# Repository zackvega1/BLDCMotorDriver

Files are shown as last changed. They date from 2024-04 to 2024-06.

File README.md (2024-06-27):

# BLDCMotorDriver
This project heavily references the code seen in the [simpleFOC repository](https://github.com/simplefoc), but is modified to run on the [Raspberry Pi Pico](https://datasheets.raspberrypi.com/pico/pico-datasheet.pdf) using [PlatformIO](https://platformio.org/).

## Prototype BLDC Driver Board
Reference this link for the prototypical BLDC driver board developing during ROB 310 Winter 2024:
[BLDC Motor Driver Board](https://u.easyeda.com/account/user/projects/index/detail?project=8bae73a7920e45f9aaeda30bf190f509&listType=all)

Table of contents
=================
<!--ts-->

   * [IMPORTANT: USB driver](#important-usb-driver-to-flash-platformio-firmware-to-pi-pico)
   * [PlatformIO Setup](#platformio-setup)
   * [Results](#initial-testing-results)
<!--te-->

## IMPORTANT USB driver to flash PlatformIO firmware to Pi Pico 
If you don't do the following steps on your Pi Pico you'll likely encounter [this error](https://community.platformio.org/t/upload-error-1-on-pio-with-raspberry-pi-pico/36841).

1. Download the [Zadig USB driver installer](https://zadig.akeo.ie/)
2. Connect your Pico to your computer with a USB cable
3. Hold BOOTSEL on your Pico
4. Run Zadig and for RP2 Boot (Interface 1) install `libusb-win32 (v1.2.7.3)` or `WinUSB (v6.1.7600.16385)` \
   &rarr; we were able to get the firmware flashing to work with `libusb` but if you have issues try `WinUSB`
   

Once you have installed the USB driver of your choice on the Pico, perform the following steps when you want to reflash firmware:
1. Build your project in PlatformIO
2. Hold BOOTSEL on your Pico and power cycle
3. Manually drag `.pio/build/pico/firmware.uf2` to the mounted Pico drive

## PlatformIO Setup 

PlatformIO is the platform used to compile and build for the Raspberry Pi Pico. Follow the instructions below to install PlatformIO:

1. **Download [VSCode](https://code.visualstudio.com/download).**

2. **Open the Extension Manager:**
   
   Extension Manager

4. **Search for PlatformIO and install it:**
   
   Search for PlatformIO
   *Note: If you have not previously installed it, you'll see an "Install" button.*

5. **Restart VSCode.**
   Once restarted, you should see the PlatformIO icon on the left taskbar:

   PlatformIO Icon

6. **Confirmation:**
   If you see this icon, PlatformIO is successfully installed.

7. **For more information about PlatformIO, refer to the [documentation](https://platformio.org/).**

## Running the Code

1. **Clone or download the repository.**

2. **Open VSCode and click on the PlatformIO Icon.**

   PlatformIO Icon

4. **Your screen should look like this:**

   PlatformIO Screen

6. **Click on "Open Project".**
   
   Open Project

8. **Locate the directory where you saved your repository and click "Open".**
   *Note: Make sure to open the folder titled "BLDC".*

9. **PlatformIO will begin installing all necessary dependencies. This may take some time.**

10.**Once PlatformIO finishes installing everything click the build button in project tasks, this will compile the code. This will take a very long time on your first compile and be faster after that.**



### Place the Pico in BOOTSEL Mode by unplugging it, holding down the BOOTSEL button, then plugging it back in. You should see a mounted drive appear on your computer. 

11. **Go to the directory of repository. In the pico/build folder you should see a firmware.uft file once PlatformIO has finished buliding your code. Drag this to the pico**
12. **The Pico should then eject and your code will have been uploaded to the pico**

## Initial Testing Results

### Random Setpoint Position Control

https://github.com/zackvega1/BLDCMotorDriver/assets/79417604/a46cdf18-8f71-4b4d-b843-c2d0ab8e5b1c

### Sine Wave Trajectory

https://github.com/zackvega1/BLDCMotorDriver/assets/79417604/abbf2bf4-174d-46f4-b3fa-4214b0e3bb09

### Compliant Operation (Torque Limited)

https://github.com/zackvega1/BLDCMotorDriver/assets/79417604/30a29a10-5d14-485c-8b83-cfc31a08579d

## Single Motor Motor Driver Board

Schematic: 
SCH_SingleMotor_2024-06-26

Top Layer View:

3D_SingleMotor_2024-06-26

Contact `zvega` or `celwell20` for EasyEDA link

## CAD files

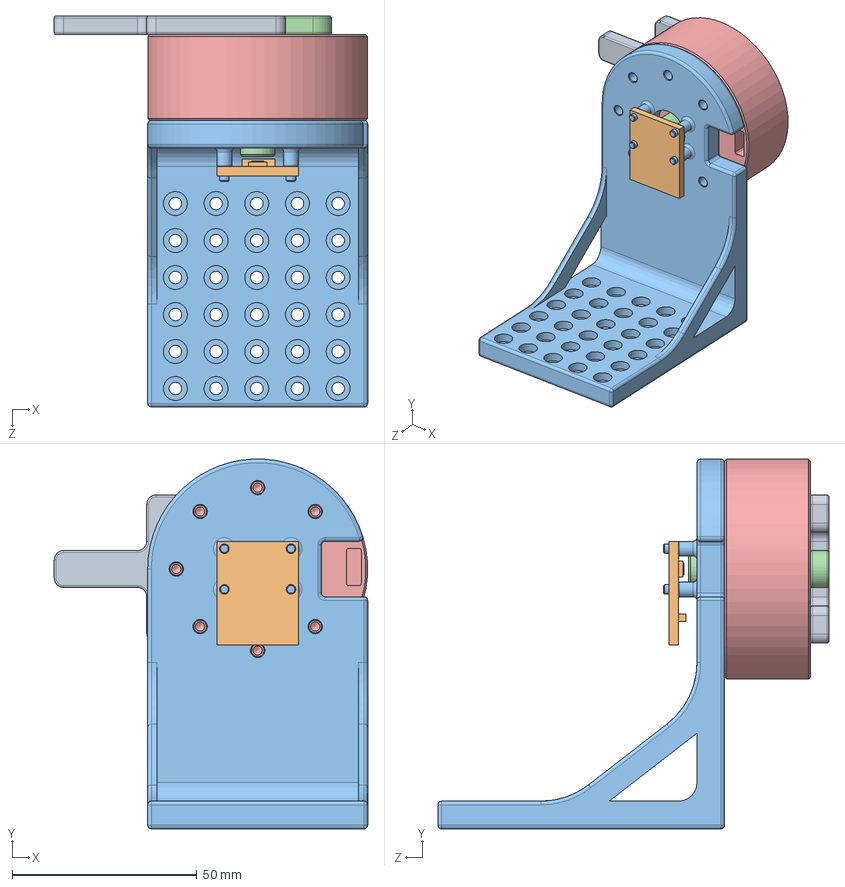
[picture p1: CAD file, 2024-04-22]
CAD/GM5208_CAD/GM5208__ENCODER_ASM.SLDASM
84.7 x 100.0 x 105.7 mm
GM5208-24_PART
GM5208_ROTOR_MAGNET_ADAPTER
GM5208_STATOR_ENCODER_ADAPTER
encoder_board
GM5208_TUNINGFORK

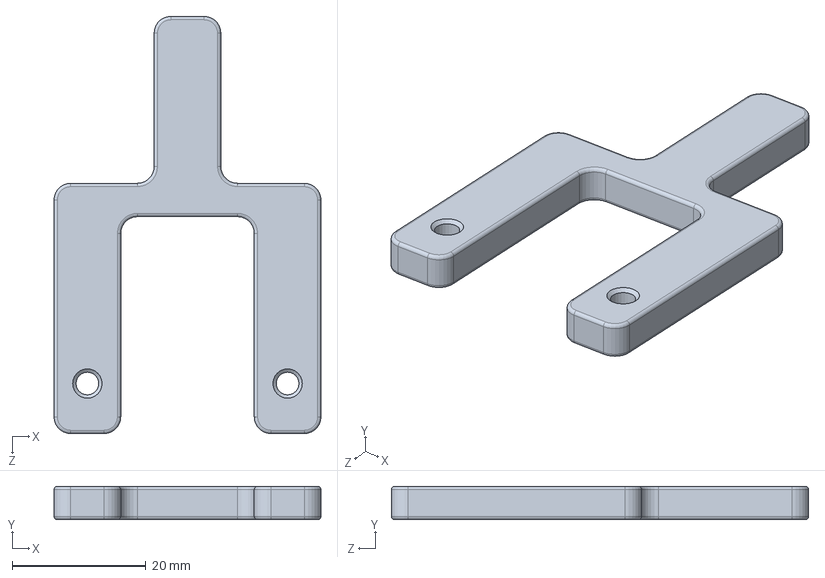
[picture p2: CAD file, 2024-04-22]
CAD/GM5208_CAD/GM5208_TUNINGFORK.SLDPRT
40.0 x 5.00 x 62.5 mm

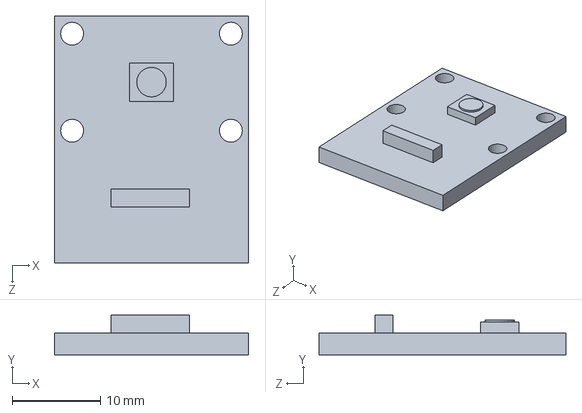
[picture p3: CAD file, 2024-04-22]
CAD/GM5208_CAD/encoder_board.SLDPRT
22.0 x 4.50 x 28.0 mm

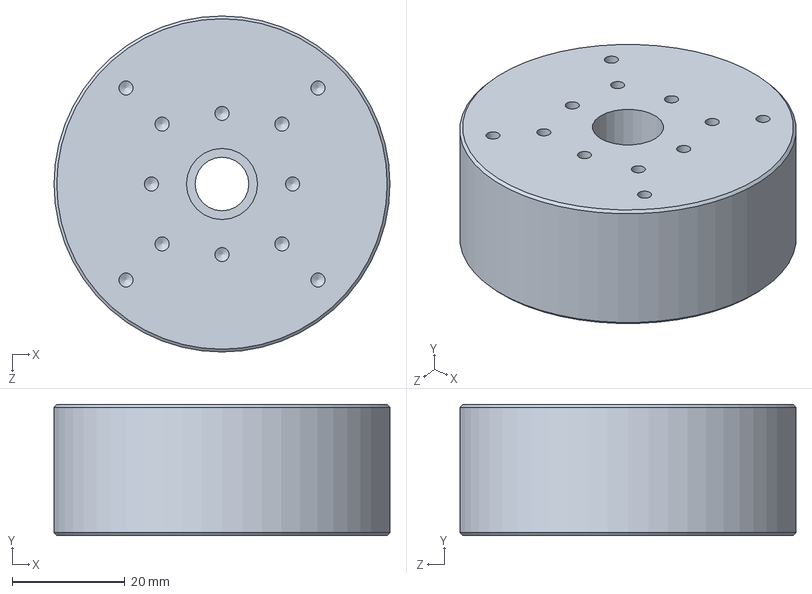
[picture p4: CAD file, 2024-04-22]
CAD/GM5208_CAD/GM5208-24_PART.SLDPRT
59.5 x 23.2 x 59.5 mm

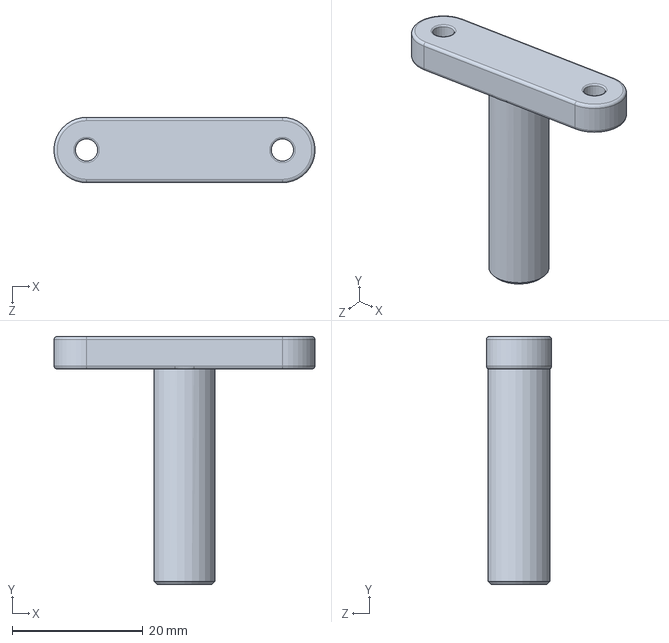
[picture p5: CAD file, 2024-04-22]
CAD/GM5208_CAD/GM5208_ROTOR_MAGNET_ADAPTER.SLDPRT
40.0 x 38.0 x 10.0 mm

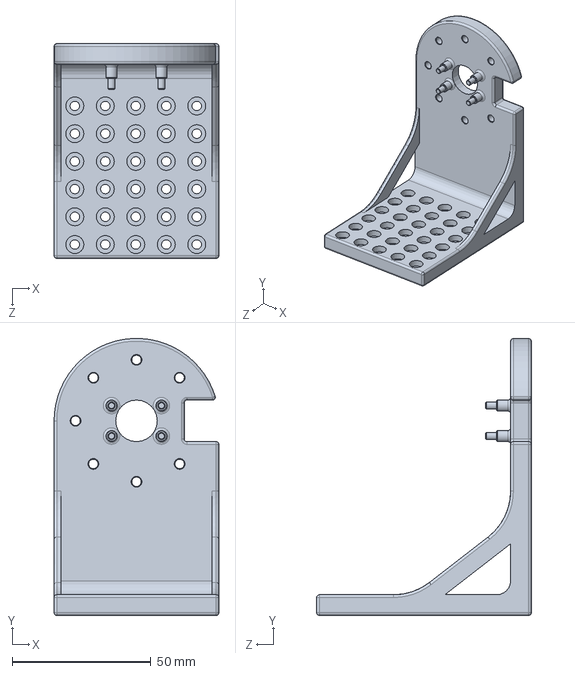
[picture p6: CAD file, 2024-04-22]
CAD/GM5208_CAD/GM5208_STATOR_ENCODER_ADAPTER.SLDPRT
59.5 x 100.0 x 77.5 mm

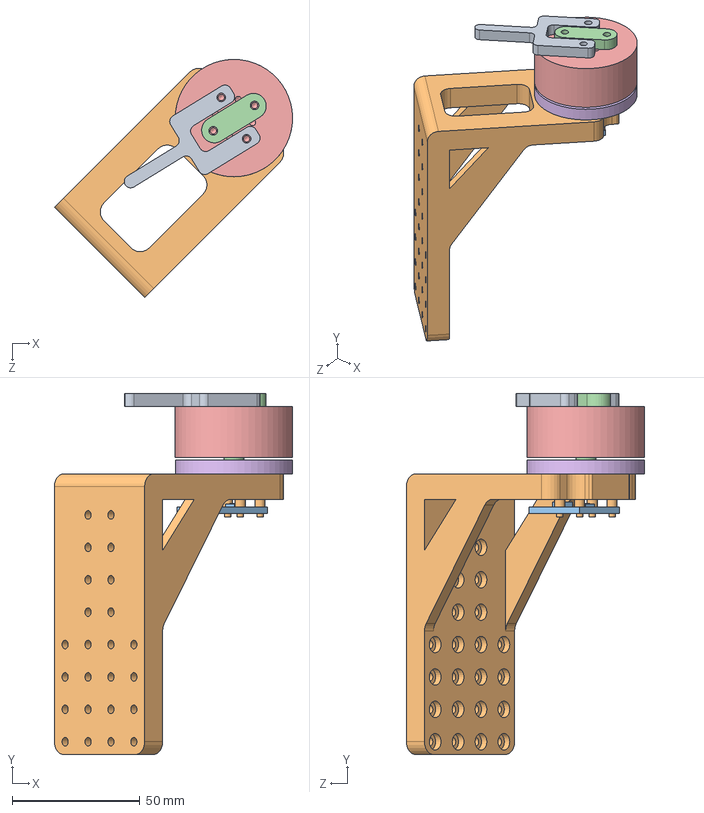
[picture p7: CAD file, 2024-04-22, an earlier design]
CAD/old_motor_cad/motor_encoder_assembly.SLDASM
93.4 x 141.5 x 93.4 mm
stator
rotor
magnet_mount
encoder_board
encoder_adapter_rev2
tuning_fork

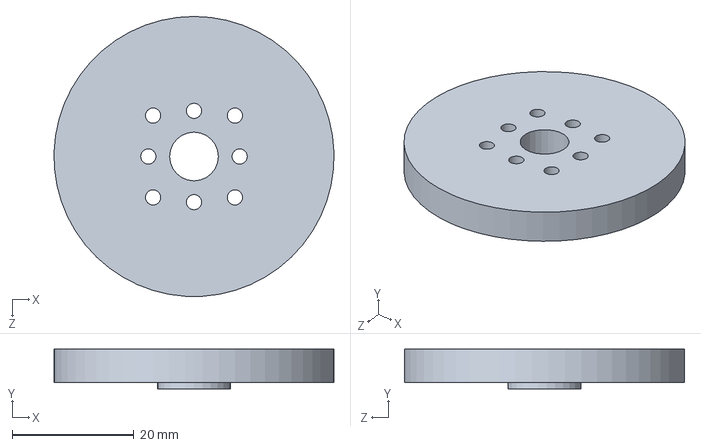
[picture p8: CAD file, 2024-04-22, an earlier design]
CAD/old_motor_cad/stator.SLDPRT
46.0 x 6.50 x 46.0 mm

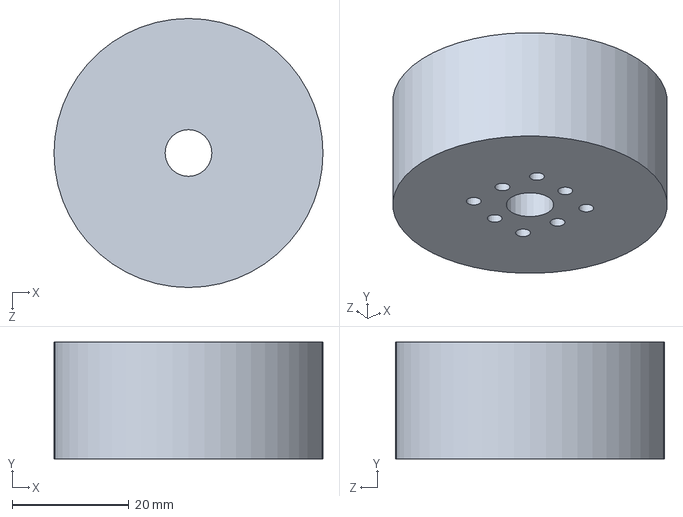
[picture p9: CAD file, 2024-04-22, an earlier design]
CAD/old_motor_cad/rotor.SLDPRT
46.0 x 20.0 x 46.0 mm

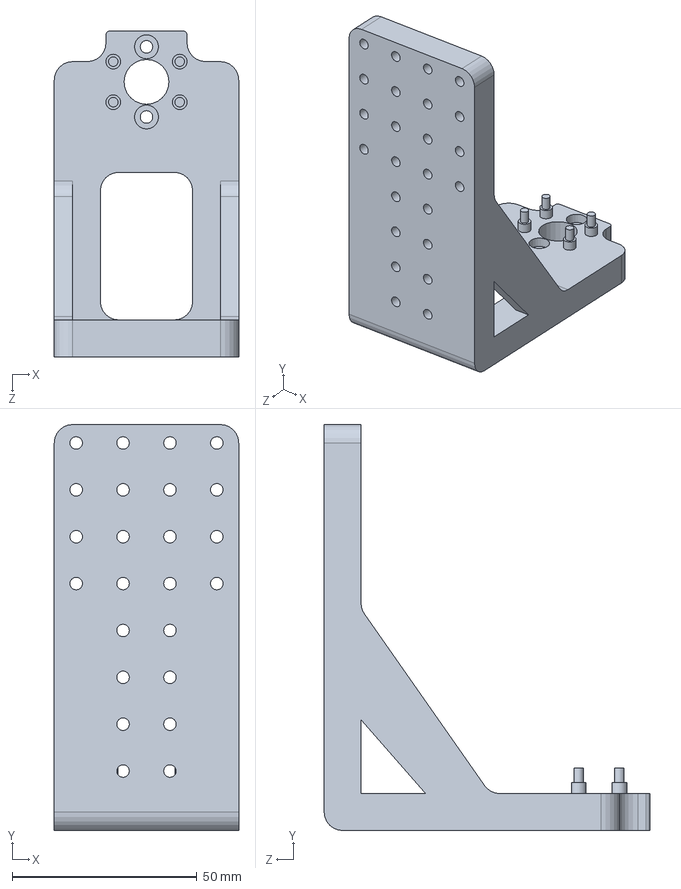
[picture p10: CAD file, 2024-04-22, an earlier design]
CAD/old_motor_cad/encoder_adapter_rev2.SLDPRT
50.0 x 110.0 x 88.2 mm

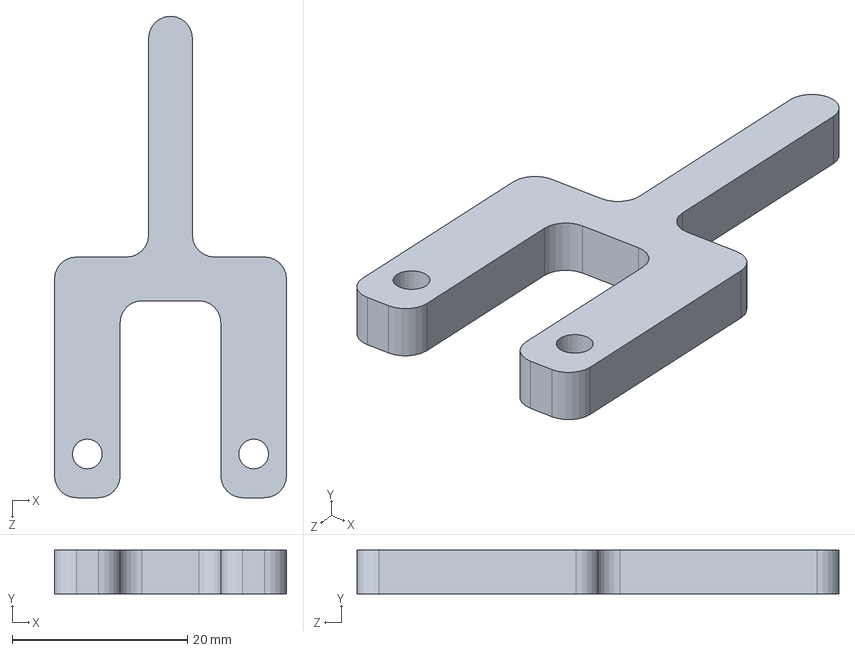
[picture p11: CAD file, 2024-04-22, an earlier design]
CAD/old_motor_cad/tuning_fork.SLDPRT
26.5 x 5.00 x 55.0 mm

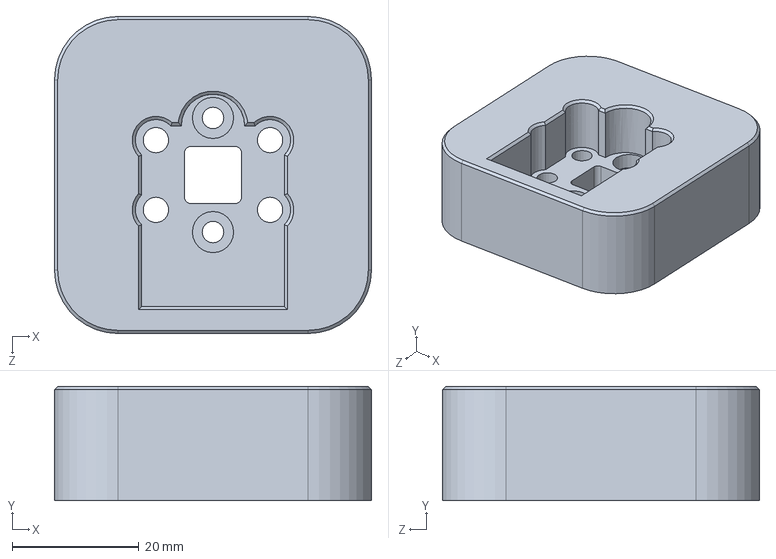
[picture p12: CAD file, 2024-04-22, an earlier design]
CAD/old_motor_cad/encoder_stator_adapter.SLDPRT
50.0 x 18.0 x 50.0 mm

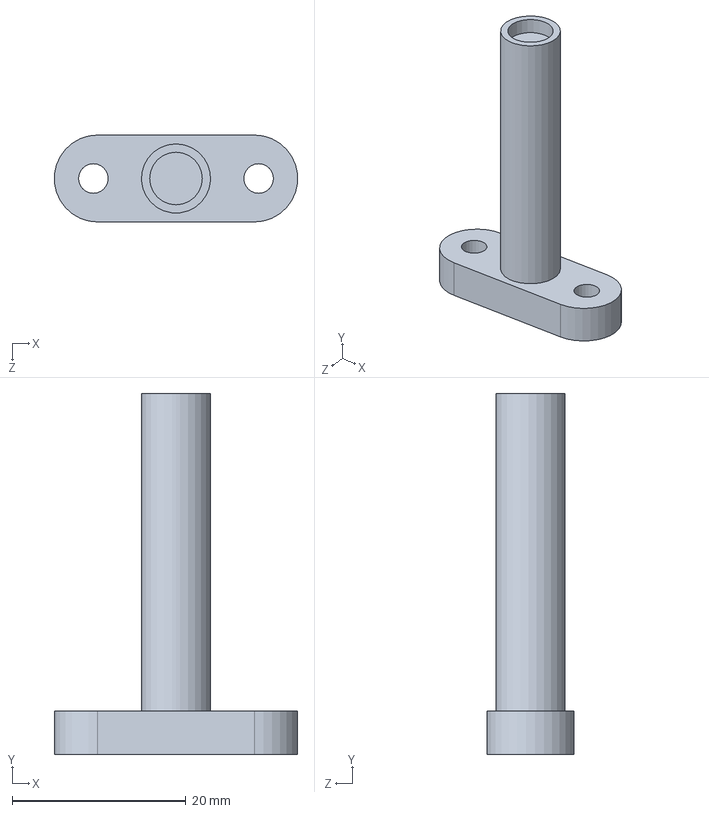
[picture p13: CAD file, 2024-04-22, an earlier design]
CAD/old_motor_cad/magnet_mount.SLDPRT
27.9 x 41.5 x 10.0 mm

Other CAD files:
CAD/GM5208_CAD/GM5208_ROTOR_MAGNET_ADAPTER.STL
CAD/GM5208_CAD/GM5208_STATOR_ENCODER_ADAPTER.STL
CAD/GM5208_CAD/GM5208_TUNINGFORK.STL

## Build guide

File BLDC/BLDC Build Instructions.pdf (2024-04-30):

Software Setup
Please follow the software setup instructions in our GitHub (https://github.com/zackvega1/BLDCMotorDriver) to update the drivers on the Pico properly, install PlatformIO, and run the code on the Pico. Be sure to update the drivers on the Raspberry Pico. Without this step, the project code will not work.

Hardware Assembly
Parts list for the BLDC Motor Driver Project:
- 1x AS5047 Magnetic Absolute Encoder
- 1x GM5208 Brushless Gimble Motor
- 1x Raspberry Pico
- 1x Brushless Bros Inc. PCB
- 1x 8-pin Wire Harness
- 1x 3-pin Wire Harness
- 1x power supply
- 1x 3D Printed Stator-Encoder Adapter
- 1x 3D Printed Rotor Magnet Adapter
- 1x 3D Printed “Tuning Fork”
- 1x 3D Printed PCB mount
- 8x 3M Bolts

Tools:
- Phillips Head Screwdriver
- Clamps (To clamp the motor mount to a table)

Instructions:
- 3D Print all necessary parts
- All CAD files can be found on our Github here (https://github.com/zackvega1/BLDCMotorDriver/tree/main/CAD/GM5208_CAD)
- All parts except the PCB mount and tuning fork were printed on a Form 2 Formlabs resin printer for dimensional accuracy
- The PCB mount and tuning fork were printed on an FDM Creality Ender 3
- Mount the Stator-Encoder Adapter to the GM5208 Motor’s stator using 4 10mm 3M bolts

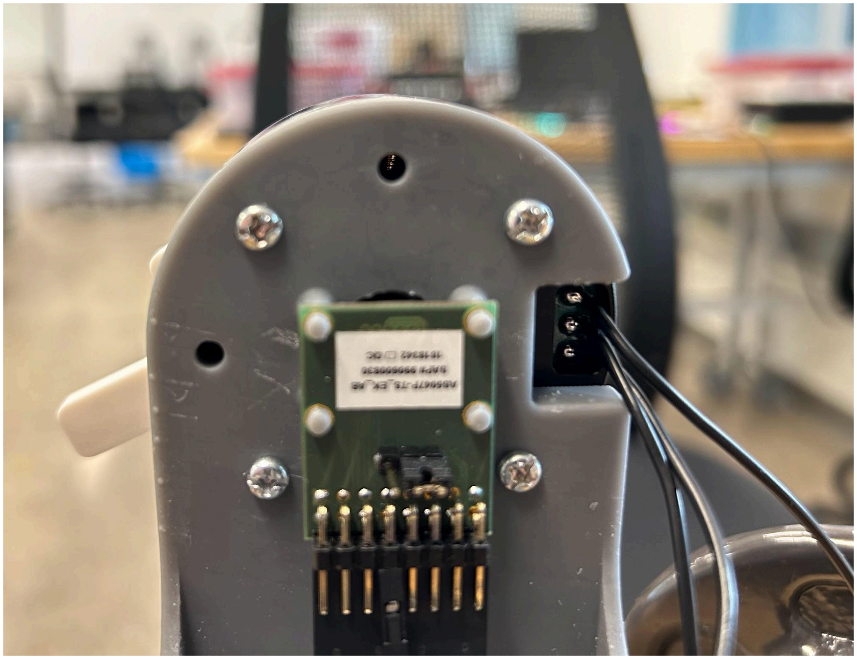
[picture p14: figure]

- Place the magnet disk for the encoder in the Rotor Magnet Adapter (press fit)
- Mount the Rotor Magnet Adapter to the GM5208 Motor’s rotor using 2 3M bolts
- Mount the Tuning Fork to the GM5208 Motor’s rotor using 2 3M bolts

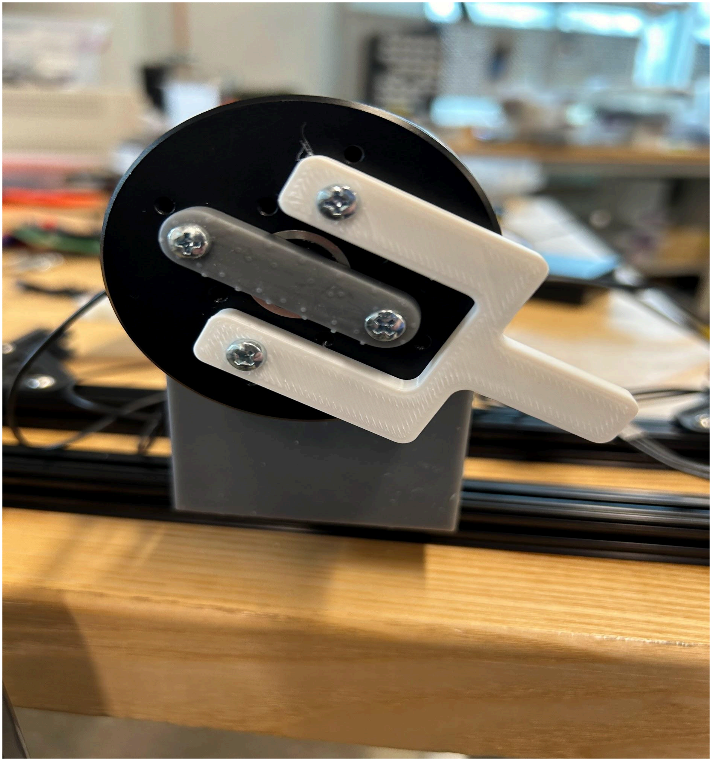
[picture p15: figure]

- Place the AS5047 Encoder chip on the Stator-Encoder Adapter by sticking the placement stubs through the mounting holes on the encoder chip
- Place the PCB board in the PCB mount
- Connect one side of the 8-pin wire harness to the bottom row of pins on the encoder chip (should have CSn, CLK, MISO, and MOSI pins along with power/ground pins)
- Connect the opposite side of the 8-pin wire harness to the PCB 8-pin female header pin connector

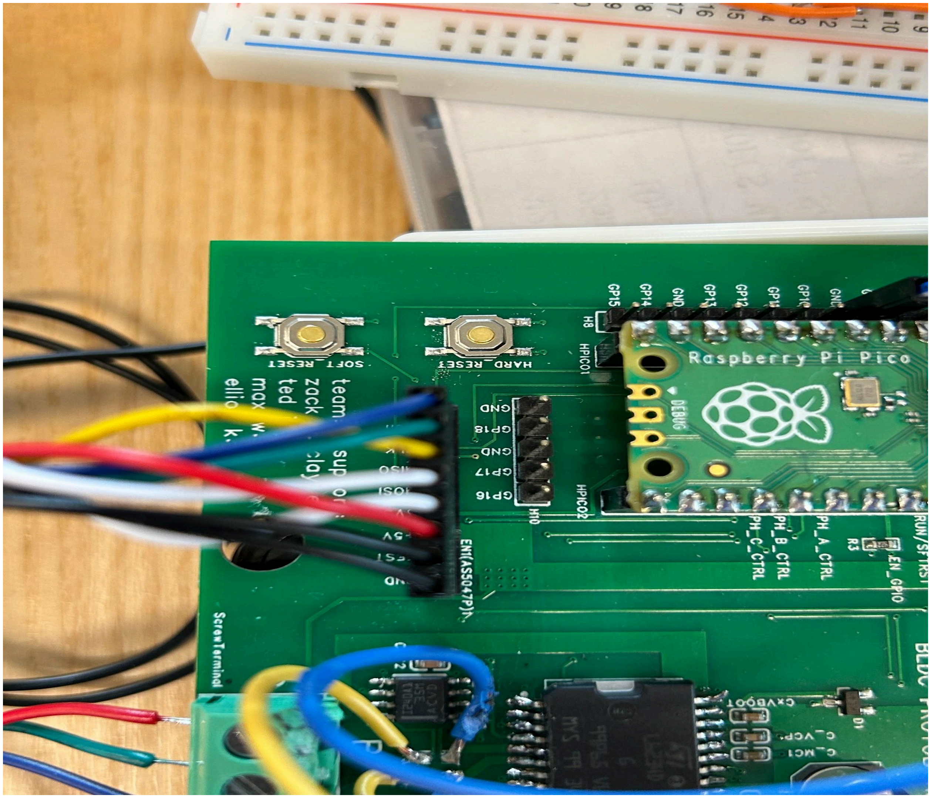
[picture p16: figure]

- Place the Raspberry Pico in the 20 female header pin connectors on the PCB
- Note about the PCB: our photos include the use of a breadboard wired to the PCB to replace resistors that had incorrect values during PCB production. If the shunt resistors R4 and R5 are 5 megaohms, this change will need to be made. If not, this change is not necessary. For the sake of brevity, we have left this change out of this document as it should not be necessary
- Connect the connector side of the 3-pin wire harness to the GM5208 wires
- Connect the opposite side of the 3-pin wire harness to the PCB by securing it in the 3-pin screw terminal

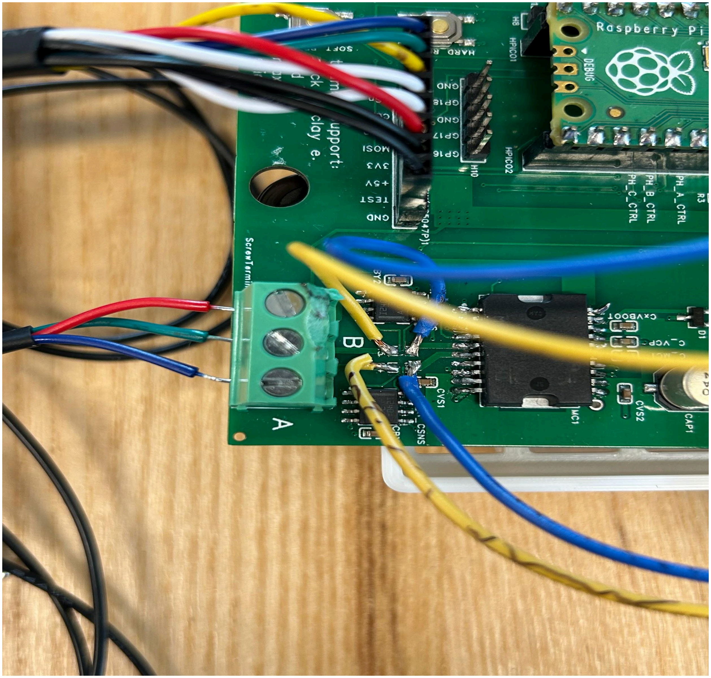
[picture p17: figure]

- Plug in the Power Supply (USB Battery) the barrel jack connector
- Connect micro USB cable to the Raspberry Pico for programming

Quick Startup
Once you’ve completed the software and hardware setup, pull the code from our GitHub to your local machine and set it up as a PlatformIO project. Follow the instructions in the software setup section to build the code and flash it onto the Raspberry Pico. The library of code will give you the ability to do velocity control or position control with this setup. In velocity control mode, you can set a speed setpoint and have the motor spin at the desired speed in (rad/s). In position control mode, you can set positional setpoints (in radians) and have the motor turn to those setpoints.

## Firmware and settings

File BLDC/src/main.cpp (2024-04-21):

#include "Arduino.h"
#include "SPI.h"
#include "SimpleFOC.h"
#include "SimpleFOCDrivers.h"
#include "encoders/as5047/MagneticSensorAS5047.h"


#define SPI_2_MISO  4
#define SPI_2_MOSI  3
#define SPI_2_SCK   2
#define SENSOR1_CS  5 

// magnetic sensor instance - SPI

MagneticSensorAS5047 sensor(SENSOR1_CS, true);
MbedSPI spi2(SPI_2_MISO, SPI_2_MOSI, SPI_2_SCK);

// BLDC motor & driver instance
BLDCDriver3PWM driver = BLDCDriver3PWM(21, 20, 19, 22);
BLDCMotor motor = BLDCMotor(11, 9.75);

// commander interface
Commander command = Commander(Serial);
void onTarget(char* cmd){ command.target(&motor,cmd); }
void onMotor(char* cmd){ command.motor(&motor, cmd); }
void onMotion(char* cmd){ command.motion(&motor,cmd); }

void setup() {
  spi2.begin();
  sensor.init(&spi2);
  // initialise magnetic sensor hardware
  sensor.init();
  // link the motor to the sensor
  motor.linkSensor(&sensor);

  // driver config
  // power supply voltage [V]
  driver.voltage_power_supply = 12;
  driver.init();
  // link driver
  motor.linkDriver(&driver);

  // set control loop type to be used
  motor.controller = MotionControlType::angle;

  // contoller configuration based on the control type 
  motor.PID_velocity.P = .125;
  motor.PID_velocity.I = 7;
  // motor.PID_velocity.D = 0.001;
  // default voltage_power_supply
  motor.voltage_limit = 10;
  motor.PID_velocity.output_ramp = 1000;


  // velocity low pass filtering time constant
  motor.LPF_velocity.Tf = 0.045;

  // angle loop controller
  motor.P_angle.P = 8.0;
  motor.velocity_limit = 50;
  motor.current_limit = .3;
  
  Serial.begin(115200);
  motor.useMonitoring(Serial);

  // initialise motor
  motor.init();
  // align encoder and start FOC
  motor.initFOC();

  // set the inital target value
  motor.target = M_PI/4;

  // define the motor id
  command.add('A', onMotor, "motor");
  command.add('M',onMotion,"motion control");
  
  // Run user commands to configure and the motor (find the full command list in docs.simplefoc.com)
  Serial.println(F("Motor commands sketch | Initial motion control > torque/voltage : target 2V."));
  motor.monitor_variables = _MON_TARGET | _MON_VEL | _MON_ANGLE ; 
  motor.monitor_downsample = 100; 
  _delay(1000);
}


//float target_angle = sin(0);
//long timestamp_us = _micros();
//float target_velocity = 2; // 2Rad/s ~ 20rpm
//float d_T = .00;

void loop() {

  motor.loopFOC();
  
  //motor.move(2*sin(d_T));
  motor.move();


  // user communication
  command.run();
  motor.monitor();
  //d_T += .0001;
}

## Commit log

2024-04-21 PID Tuning
2024-04-22 added CAD files for old motor encoder mount and GM5208 encoder mount
    [GM5208-24_PART.SLDPRT, GM5208_ROTOR_MAGNET_ADAPTER.SLDPRT, GM5208_ROTOR_MAGNET_ADAPTER.STL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]
2024-06-27 added rev1 pcb images
